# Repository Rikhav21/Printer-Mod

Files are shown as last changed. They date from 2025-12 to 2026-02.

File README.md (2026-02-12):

# Laser cutting printer
## Overview
I basically designed and build a laser cutting attatchement for a toolhead of a 3d printer. You could probably get this to work on any printer that runs klipper, but I modded my custom printer




## The build
For the build all that you would need to do is attatch the laser to the toolhead using a bracket, which I just printed in PLA. You are most likely going to have  You can look at the CAD [here](https://cad.onshape.com/documents/d856a3708ade0f004ee6e4d1/w/7b963df3d5215184ce110ce8/e/33774b02b25fc0851c569ffd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)



## The electronics
For the electronics, all you have to do is connect the laser PSU to it's controller. Then I connected the ground and controller pin of my mainboard to the DC in and ground on our laser controller. Finally I just plugged in the lasser pins to the controlboard and that should be all of the wiring.
530048269-61fd2402-6133-4082-97aa-afdab45ca0bf

## The firmware
After that you can test it by uploading my new printer config. Really all you need to know is what GPIO you are using to connect it to your printer, (I used 20) and then just adust my macros to turn it on or off. I would recommend starting at a really low value, and make sure that you always have your glasses on.
After that you are going to have to download change.py and input your gcode file. I used LaserGRBL and it exported as a .nc. As long as you name it input.nc you should get a folder named output.gcode that youcan upload to klipper. After that you should ust be able to run output.gcode and it will engrave your image!

530050401-e7ebefd4-ec5e-4e9c-b518-6d1618c2aaa8



## BOM

| Item | Description | Supplier Link | Unit Price (USD) | Qty | Total |
| ---: | --- | --- | ---: | --: | ---: |
| 1 | Laser Module (≈80W optical class, AliExpress listing) | [AliExpress](https://www.aliexpress.us/item/3256804434878907.html) | $40.00 | 1 | $40.00 |
| 2 | Power Supply Unit (PSU) | [AliExpress](https://www.aliexpress.us/item/3256807006443600.html) | $12.00 | 1 | $12.00 |
| | **Total Cost** | | | | **$52.00** |

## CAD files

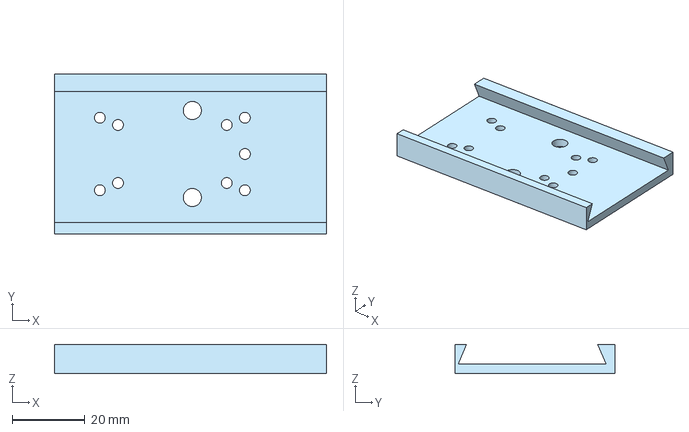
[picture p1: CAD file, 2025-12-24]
Laser attatch.step
75.0 x 44.0 x 8.00 mm

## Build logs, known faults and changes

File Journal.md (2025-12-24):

# Laser cutter 
#### By @Rikhav
Time spent 32 and a half hours
## Day 1
So today I mainly ust worked on research took an inventory on parts that I had, and sort of thought about how to build this thing. I found something really cool where someone
[attatches a laser cutter to their A1 mini](https://www.reddit.com/r/BambuLab/comments/1oi44fl/i_turned_my_bambu_a1_mini_into_a_mini_laser_cutter/) 
so I was thinking that I can domehitn gsimilar to that. Today I was mainly looking at wiring, how I would actually do it, adustability etc.



Total time spent : 3 and a half hours.
## Day 2
So today I went more down the laser cutting rabit hole and actually saw different designs that people implemented. I decided that it would probably be better if I modded mmy custom printer (inspired by the 100) instead of my bambu labs, because I ust know how it works a lot better. However, I also did realize that my laser does operate at a different voltage than the rest of my printer so I am going to have to use a seperate PSU for that. I also loked more into the mounting solutions, and I decided on a 3d printed bracket that can hold a sliding frame.


Total time spend : 4 hours.
## Day 3
Today I mainly spent time on actually getting the elctronics done, so I soldered the wires, tested connections before powering it on, because it's pretty high voltage, stuff, and triple checking that everything was wired correctly before giving it power. Here I didn't have a barrel ack for DC input to the laser controller, so instead I ust soldered on the wires to the back of the board with the exposed socket terminals. I did test it where I turned it on,a nd the laser was at 0.1% power, and I was able to see a faint blue glow so it does work. tomorrow I am going to try to mount and actually cut something.


time spent: 4 hours

## Day 4
Today I ust wanted to finish the assembly portion and try powering everything on. it turned out that actually connecting the laser controll board to the SKR pico was a little bit harder than I thought, because the board was out of reach, and the wires to the laser restricted its movement so I had to make them longer. I had to redeigsn the mount because the first one did  not fit that well,a nd I had to print at about 50% infill because it was supporting almost the entire weight of the laser. Although the toolhead is now heavier, it doe snot seem to actually change the movement of the toolhead that much.




time spend: 3 and a half hours.

## Day 5
Today I tried to do firmware. I actually had a lot of trouble figuring out how to controll the laser through klipper, and so I ended up just addressing the GPIO pin directly through macros to turn the GPIO on or off. this actually toook a lot longer than I expected, but the laser is turning on at 5% of full power, and is able to start burning wood.I also researched a bit more about actually slicng laser G-code and I decided on uring LaserGRBL for that, but I will actually start slicing code tomorrow.

Time spent: 2 hours

## Day 6
Today was another firmware day. I tried to make it so that I can controll the amount that the laser turns on based on the value that I send it,a nd I got that macro working. Then I learned how to use LaserGRBL, and sliced my first image of a square. after exporting it, I realized that it was exported with a .nc file extensions, so I could import it into klipper, but I was not able to get it to run, I tried a few different things, but at the end it turns out that just changing the file extension to .gcode actually works perfectly. Although I was able to get the code to at least start compiling, it was still giving errors about unrecognized commands so I will look into that tomorrow.



Time spent : 3 hours

## Day 7
Today I tried to look into what was actually causing the errors, and realized that the g-code that LaserGRBL exported was actually not able to run on klipper because it did not recognize S80 or something like that sa a command, so I tried to set up macros so that klipper could tell that I was trying to turn on the laser. That didn't work either because S90 had to be written as S S-90; And I had no idea how to do that. I trid finding and replacing all of those, however I got some complaints that I think I can fix by moving the macros to a new line, but I am going to work on that tommorrow.

Time spent:  4 hours

## Day 8
Today I continued to work on the firmware for the mod, and once again it turned out harder than I expected, because after seperating all the lines, you need to add semi colos back to the end of the line that you seperated, so instead I spend an hour writing a python script to do that for me, and how I am finally able to execute the code that I sliced with lightburn, as my script ust inputs the .nc file that you get out of LaserGRBL, and converts it to a .gcode file that klipper coudl read. I hadm't donw any calibration yet, but the laser was able to mark the surface of the scrap wook.



Time spent 4 and a half hours.

## Day 9
Today was mainly ust a trouble shooting day, I updated the code some more, added macros, and did some more stuff with the firmware, and edited the laser positioning so that now I was actually able to engrave into some wood. I wasn't able to cut it, because my woord is really dense, but I might gut some plywood or something else to lasercut later.




Time spent: 4 hours

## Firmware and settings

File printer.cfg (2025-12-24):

[include mainsail.cfg]
[virtual_sdcard]
path: /home/pi/printer_data/gcodes
on_error_gcode: CANCEL_PRINT

[mcu]
serial: /dev/serial/by-id/usb-Klipper_rp2040_504450612072621C-if00
restart_method: command

[printer]
kinematics: corexy      # tell klipper it's a corexy
max_velocity: 100       # these are all intentionally slow for initial testing purposes
max_accel: 1000         # ^
max_z_velocity: 15      # ^
max_z_accel: 50         # ^

[force_move]
enable_force_move: true     # allows us to move the motors without homing

[stepper_x]
step_pin: gpio11
dir_pin: !gpio10
enable_pin: !gpio12
rotation_distance: 35
microsteps: 64
endstop_pin: tmc2209_stepper_x:virtual_endstop
position_min: -1
position_endstop: 100
position_max: 100
homing_speed: 40
homing_retract_dist: 0

[tmc2209 stepper_x]
uart_pin: gpio9
tx_pin: gpio8
uart_address: 0
run_current: 0.8
stealthchop_threshold: 999999
diag_pin: ^gpio4
driver_SGTHRS: 120
interpolate: true

[stepper_y]
step_pin: gpio6
dir_pin: gpio5
enable_pin: !gpio7
microsteps: 64
rotation_distance: 35
endstop_pin: tmc2209_stepper_y:virtual_endstop
homing_retract_dist: 0
position_min: 0
position_endstop: 154
position_max: 154
homing_speed: 40
homing_positive_dir: true

[tmc2209 stepper_y]
uart_pin: gpio9
tx_pin: gpio8
uart_address: 2
run_current: 0.8
stealthchop_threshold: 999999
diag_pin: ^gpio3
driver_SGTHRS: 120
interpolate: true

[stepper_z]
step_pin: gpio19
dir_pin: gpio28
enable_pin: !gpio2
microsteps: 16
rotation_distance: 8
full_steps_per_rotation: 200
endstop_pin: tmc2209_stepper_z:virtual_endstop
#position_min: -6
position_min: -21
position_max: 140
homing_speed: 4
#position_endstop = 0.650
homing_retract_dist: 0

[tmc2209 stepper_z]
uart_pin: gpio9
tx_pin: gpio8
uart_address: 1
run_current: 0.7
diag_pin: ^gpio25
driver_SGTHRS: 71
stealthchop_threshold: 999999


[extruder]
step_pin: gpio14
dir_pin: gpio13
enable_pin: !gpio15
microsteps: 16
rotation_distance: 22.596444
gear_ratio: 50:17
full_steps_per_rotation: 200
nozzle_diameter: 0.4
max_power: 0.35
filament_diameter: 1.75
heater_pin: gpio23
sensor_type: ATC Semitec 104NT-4-R025H42G
sensor_pin: gpio27
#control: pid
#pid_Kp: 22.2
#pid_Ki: 1.08
#pid_Kd: 114
min_temp: 0
max_temp: 300
max_extrude_cross_section:2
pressure_advance: 0.354
max_extrude_only_distance: 500
max_extrude_only_velocity: 120
max_extrude_only_accel: 800
instantaneous_corner_velocity: 20
min_extrude_temp: 0   # Only for testing. Should be increased to 190+ when done configuring.

[tmc2209 extruder]
uart_pin: gpio9
tx_pin: gpio8
uart_address: 3
run_current: 0.8
stealthchop_threshold: 999999
##### HOMING MACROS START #####

[gcode_macro G28]
rename_existing: G280
gcode:
  M80
  SET_KINEMATIC_POSITION Z=0
  G90
  G1 Z5 F200
  SENSORLESS_HOME_X
  SENSORLESS_HOME_Y
  SENSORLESS_HOME_Z

[gcode_macro SENSORLESS_HOME_X]
gcode:
    SENSORLESS_DELAY
    # Home
    G280 X
    # Move away
    G1 X{ printer.toolhead.axis_maximum.x/2 } F6000

[gcode_macro SENSORLESS_HOME_Y]
gcode:
    SENSORLESS_DELAY
    # Home
    G280 Y
    # Move away
    G90
    G1 Y{ printer.toolhead.axis_maximum.y/2 } F6000

[gcode_macro SENSORLESS_HOME_Z]
gcode:
    SENSORLESS_DELAY
    # Home
    G1 X{ printer.toolhead.axis_maximum.x/2 } Y{ printer.toolhead.axis_maximum.y } F6000
    G280 Z
    SET_KINEMATIC_POSITION Z=1
    G1 Z0 F120
    G1 Z5 F120
    SENSORLESS_DELAY
    G280 Z
    G1 Z5 F120   # Make sure we clear the toolhead
    G1 X{ printer.toolhead.axis_minimum.x +5 } Y{ printer.toolhead.axis_maximum.y -2 } F6000


[gcode_macro SENSORLESS_DELAY]
gcode:
    # Pause to ensure driver stall flag is clear
    G4 P2000

[gcode_macro M80]
gcode:
  SET_STEPPER_ENABLE STEPPER=stepper_x ENABLE=1
  SET_STEPPER_ENABLE STEPPER=stepper_y ENABLE=1
  SET_STEPPER_ENABLE STEPPER=stepper_z ENABLE=1

##### HOMING MACROS END #####
[gcode_macro START_PRINT]
gcode:
   {% set BED_TEMP = params.BED|default(60)|int %}
   {% set EXTRUDER_TEMP = params.HOTEND|default(200)|int %}
   CLEAR_PAUSE

   {% if printer.heater_bed.temperature < (BED_TEMP-10) %}
      M140 S{BED_TEMP-10}
   {% endif %}

   G90 ; use absolute coordinates
   G92 E0 ; reset extruder hsaiuf
   
   {% if "xyz" not in printer.toolhead.homed_axes %}
      G28 ; home all axis
   {% endif %}
   G1 ; set units to millimeters

   {% if printer.heater_bed.temperature < (BED_TEMP-10) %}
      M190 S{BED_TEMP-10}
   {% endif %}

   M104 S{EXTRUDER_TEMP}
   M190 S{BED_TEMP}
   M109 S{EXTRUDER_TEMP}
   DRAW_LINE SPEED=1200
[gcode_macro END_PRINT]
gcode:

    # Move nozzle away from print while retracting
    G91 ;releative positioning
    G1 E-1 F2700 ;Retract a bit
    G1 E-1 Z0.2 F2400 ;Retract and raise Z
    G1 X-3 Y-3 F3000 ;Wipe out
    G1 Z10 F400 ;Raise Z more

    # Turn off bed, extruder, and fan
    M140 S0
    M104 S0
    M106 S0

    G90 ; Absolute Positioning
    G1 X{ printer.toolhead.axis_minimum.x +10 } Y{ printer.toolhead.axis_maximum.y - 20 } F3600 ; Move Printer Head Out of Way

    M84 X Y E ;Disable all steppers but Z


[gcode_macro DRAW_LINE]
gcode:
    {% set SPEED = params.SPEED|default(900)|int %}
    G92 E0 ;Reset Extruder
    G1 Z1.0 F400 ;Move Z Axis up

    G1 X5.1 Y140 Z0.3 F5000  ;Move to start position
    G1 X5.1 Y40.0 Z0.3 F{SPEED} E15 ;Draw the first line
    G1 X5.4 Y40.0 Z0.3 F{SPEED} ;Move to side a little
    G1 X5.4 Y140 Z0.3 F{SPEED}.0 E30 ;Draw the second line

    G92 E0 ;Reset Extruder
    G1 Z1.0 F400 ;Move Z Axis up
    G4 P500
    G1 X8 F{SPEED} ;Move to side so it doesn't crash in to the blob

[multi_pin part_cooling]
pins: gpio17

[fan]
pin: multi_pin:part_cooling

[heater_fan hotend_fan]
pin: gpio18
heater: extruder
heater_temp: 40.0

[output_pin laser_pwm]
pin: gpio20
pwm: True
cycle_time: 0.001   # 1 kHz

[gcode_macro LASER_ON]
gcode:
    SET_PIN PIN=laser_pwm VALUE=0.13  # 5% duty cycle

[gcode_macro LASER_OFF]
gcode:
    SET_PIN PIN=laser_pwm VALUE=0.0
[gcode_macro LASER_PULSE]
gcode:
    SET_PIN PIN=laser_pwm VALUE=0.05  # 5% power for safe test
    G4 P0.2                          # wait 0.2 seconds
    SET_PIN PIN=laser_pwm VALUE=0.0   # turn off
[gcode_macro M3]
description: Laser on (constant power)
gcode:
    {% set power = params.S|default(0)|float %}
    SET_PIN PIN=laser_pwm VALUE={power / 1000.0}
[gcode_macro M4]
description: Laser on dynamic (per-line power)
gcode:
    {% set power = params.S|default(0)|float %}
    SET_PIN PIN=laser_pwm VALUE={power / 1000.0}


[gcode_macro S]
description: Laser on with power from LaserGRBL
gcode:
    {% set power = params.S|default(0)|float %}
    SET_PIN PIN=laser_pwm VALUE={power / 1000.0}


[gcode_macro M5]
description: Laser off
gcode:
    SET_PIN PIN=laser_pwm VALUE=0.0


#*# <---------------------- SAVE_CONFIG ---------------------->
#*# DO NOT EDIT THIS BLOCK OR BELOW. The contents are auto-generated.
#*#
#*# [extruder]
#*# control = pid
#*# pid_kp = 13.083
#*# pid_ki = 0.847
#*# pid_kd = 50.533
#*#
#*# [stepper_z]
#*# position_endstop = -5.535

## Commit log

2025-12-24 Add initial journal entry for laser cutter project
    Document initial research and ideas for laser cutter project.
2025-12-24 Update Journal with Day 3 progress
    Documented progress on laser cutting project and electronics setup.
2025-12-24 Document progress for Days 5 to 8 in Journal.md
    Added entries for Days 5 to 8 detailing firmware work and laser control issues.
2025-12-24 Revise Journal.md for accuracy and clarity
    Updated time spent entries and fixed typos throughout the journal. Added details about the laser cutter assembly and firmware troubleshooting.
2025-12-24 Revise journal entries and add images
    Updated journal entries for days 7 to 9, including troubleshooting and progress on laser engraving. Added images for visual reference.
2025-12-24 Update Journal with Days 6 and 7 progress
    Document progress on firmware and LaserGRBL issues, including file extension changes and g-code command recognition problems.
2025-12-24 Add README for laser cutting printer setup
    Added instructions for using a laser cutting attachment with a 3D printer.
2025-12-24 Enhance README with images and setup instructions
    Added images and clarified instructions for laser cutting printer setup.
2026-02-03 Enhance README with build and electronics details
    Added sections on build, electronics, and firmware setup for laser cutting printer.
2026-02-12 Add BOM section to README
    Added a BOM section with item descriptions and pricing.
